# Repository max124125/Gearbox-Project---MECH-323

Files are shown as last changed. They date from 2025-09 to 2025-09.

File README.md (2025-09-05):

# Gearbox Project MECH 323

<p float="left">
  
   
</p>

This project was done throughout the MECH 323 course, and had the goal of designing, assembling and 3D printing a gearbox for a small battery powered model car. 
The gearbox had to be optimized for both a top speed event and ramp climb event, and able to shift between these two gear ratios within only a few seconds of human interaction.

An image and drawing of the gearbox before being placed in the car along with
the final report and CAD files submitted for this project can be found in the section above.

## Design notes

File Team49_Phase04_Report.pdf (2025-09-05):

# Design Project

## MECH 323 Machine Design (Winter 2024) Team 49

## Team

Number | Group 49 - Section 4

## Phase

Number | Phase IIII
Group Members | | Student Number (Required) | Student Name (Optional)
| 1 | 20275181 | Charlotte Kimmins
| 2 | 20208183 | Zoe Glover
| 3 | 20228127 | Maxwell McCutcheon
| 4 | 20298597 | Sebastian Currie

## Mark

i

## Executive Summary

The gearbox design process included the design, fabrication, and assembly of a gearbox to fit into a prefabricated test car and compete in two events, a top speed event and a hill climb event. The design was created through several iterations of modeling and simulation and was optimized into a single stage shifting gearbox that exhibits two gear ratios to effectively compete in both events. Within the project, emphasis was placed on creating a gearbox with high performance metrics while adhering to constraints of the project. The final design included an input and output shaft, two pinions, two gears, bearings, and housing. Within the overall gearbox design, a shifting one stage gearbox was decided to allow for two gear ratios, a high one to maximize torque output for the hill climb, and an inversed low gear ratio to allow for maximum RPM output for the speed event. The housing was important in creating proper fitment of the transmission into the car and worked to balance structural integrity with reducing print time through a series of triangular cut outs. There were two shafts included in the design, an input and an output shaft which were designed with considerations of tolerancing, durability, and performance. These shafts have design features of cylindrical shoulders to hold gears and pinions in place, hex sections on which the gears and pinions lay with a friction fit, and a 20 mm extension from the housing with a D cut shaft to ensure proper alignment of the sprocket and applied torque to the shafts. Additionally, the design features four metal bearings on which the shafts lay which ensures limited friction in shaft rotation. Gears and pinions were chosen for their gear ratio and full depth teeth were used to enhance torque transmission and minimize slippage.

To meet design parameters and to ensure constraints such as successful and consistent performance, low print time, ease of assembly, and scalability of production there were several iterations in the evolution of the gearbox design to reach the final design as described above. Additionally, changes had to be made to the design from the previous theoretical design process and the actuation of printing and assembly. This is inclusive of optimal gear ratios initially being chosen based on performance metrics for both events from initial software modeling, however gear ratios had to be adapted due to modulus limitations and clearance issues during the final CAD preparations. Decisions to adjust the gearbox were carefully considered and weighed against other alternatives to find the best solutions. For the instance of the gear ratios, the team opted to modify the gear ratios rather than adding additional shafts thus maintaining the gearbox integrity. These choices, and the gearbox evolutions were successful and led to performance success in both events.

ii

## Table of Contents

## List of Figures

Figure 1: Fully dimensioned gear and pinion designs. With relevant parameters when machining the

Figure 2: Fully dimensioned drawing of the gear shaft. Drawing includes the front, back and right views,

Figure 3: Fully dimensioned drawing of the pinion shaft. Drawing includes the front, back and right

iii

Figure 4: Orthographic, section, and isometric views of the gearbox with all relevant design criteria shown. Such as design parameters, fully assembled housing dimensions and d-shaft protrusion distance.
| 11
Figure 5: Exploded isometric view of the fully assembled gearbox, highlighting all gearbox parts with
numbers and their respective names and quantities | 12
Figure 6: Fully dimensioned drawing of the housing’s front/ back sides. The drawing includes front, top
and isometric views, highlighting the dimensions for the bushing’s placement | 12
Figure 7: Fully dimensioned drawing of the housings left and right sides. The drawing includes front, top
and isometric views of the part | 13

## List of Tables

Table 1: Sample parts list | 6
Table 2: Technical specifications summary table | 7

## 1.0 Introduction

In the final phase of this project, Phase 4 directed the focus onto modifying the gearbox to be more suitable for 3D printing. Housing for the gear and pinion shafts were designed to meet the dimensional constraints outlined in Phase 1. Modifications of the shaft designs were made to work with a maximum limit of six standard-sized bushings. The keyway features were also changed to hexagonal profiles for better torque transmission. Consequently, the bore holes of the pinion and gear were also adapted to hexagonal profiles to match the shaft designs. This report outlines the evolution of Team 49's gearbox design specifically relating to the transition from AISI 4130 steel to plastic.

## 2.0 Gear Box Design

### 2.1 Overall

This gear box design was created to effectively compete in a high torque hill climb event and a high-speed race event. The design was iterated with factors of performance, durability, design complexity, space constraints, print time constraints and ease of assembly as paramount in the creation of the final gearbox. The finalized design consisted of a one stage shifting gearbox with two shafts, two pinions, and two gears. In this design two gear ratios could be used to optimize the performance in both the hill climb and speed events. Design constraints such as fixed shaft locations, print time, and housing dimensions governed the final design and had implications on specific parameters for the gearbox.

### 2.2 Design

As mentioned above, the overall design is a one stage, shifting gearbox with an input and output shaft and two different gear ratios. This design was chosen to maximize performance in both events, one being a hill climb which required a high output torque, and the other being a speed event, which required a low gear ratio to maximize the output rotation. For success in the hill climb, maximum torque input without causing the DC motor to stall is desired; this in conjunction with a high gear ratio increases the torque on the output shaft which allows the gearbox to climb up the hill. A maximum input torque of 1.9 Nm was used to allow for proper propulsion of the car, without causing the motor to fail, as the motor stall torque is 2.25 Nm. The gear ratio between the pinion and the gear was 2.5, which increased maximized the input torque to 3.01 Nm which led to a theoretical slip angle of 31.3°. In addition to the hill climb, a secondary gear ratio of 0.40 was used for the top speed event. In preliminary design iterations, a gear ratio of 0.61 was chosen, however, as discussed in detail below, physical space constraints and ease of assembly factors led to the top speed gear ratio being the inverse of the hill climb gear ratio. With the same input torque, a low gear ratio allows for a lower input torque and therefore an increased speed. Additionally, by lowering the gear ratio a higher RPM was found for the output shaft which in turn caused faster rotation of the car’s tires, and therefore a faster speed.

### 2.3 Housing

One factor in the gearbox design was the housing in which the transmission components were located. The purpose of the housing was to effectively contain the pinions, gears, and shafts and to have the gearbox fit snugly into the prefabricated car. With this constraint, care was taken to ensure that proper dimensioning and geometry were used in the construction of the housing. There were four bushings located within the housing to fit the input and output shafts on both sides of the housing which worked to reduce the friction on the shafts and housing. An additional consideration for the housing was in the print time required to construct the housing walls. It was important to consider durability in the housing during testing as torque applied to the shafts could apply a force on the housing while balancing the necessity of cutouts to reduce print time. With these factors paramount, triangular cutouts were utilized to maintain the structural integrity of the housing while also reducing print time. Ease of assembly and disassembly was also considered in the design of the housing as the housing repeatedly must be constructed and deconstructed during the geartrain assembly.

### 2.4 Shafts

Two shafts, as input and an output shaft each with a pinion and gear were utilized in the gearbox design. These shafts had several shapes across the length with cylindrical shoulders in place to keep the gears and pinions where desired, hex sections where the pinions and gears sit, and a 20 mm extension from the gearbox housing with a D cut to ensure proper fitment of the sprockets which actuate rotation of the wheels. Tolerance was of importance for the shafts as there were several sections of friction fit along the shaft. These consisted of the shaft inside the bushing, a preset dimension, the pinions and gears on the hex sections, and the sprockets on the D cut shaft extension. Had the shafts been dimensioned improperly, successful performance in events would not be possible. A concern for the shafts was the strength under applied torque, especially in sections, such as the D cut, where the shaft had a small diameter. This is of concern as there is a large, applied torque to the output shaft in the hill climb and an insufficient shaft diameter could lead to shaft failure by mechanism of shear.

### 2.5 Pinions and Gears

The design utilizes two gears and two pinions in the one stage shifting gearbox to transmit torque for each of the events. By using an inverse gear ratio for both events, there is simplicity in production which is an asset for any form of mass production of a gearbox of this design. Additionally, the chosen gear ratios allowed for the use of full depth teeth, rather than stub, as the transmission of torque is not high enough to be of concern for breakage of teeth. This attribute of the pinions as gears has positive effects on the construction of the gearbox as there is increased contact between gears and pinions and there is a decreased risk of slippage, especially when utilizing a friction fit. For the hill climb event, the pinion has eth and the corresponding gear has 37 teeth and the inverse is true for the top speed event.

### 2.6 Additional Performance Parameters

A module of 1.5 mm was utilized for the gearbox design. This module allowed for an increased number of teeth on the gears and pinions without a notable increase in the physical space consumed by each member. Additionally, in the gearbox design a pressure angle of 20 ˚ which represents the angle between the tooth face and the gear wheel tangent, dictating the point of impact for applied tangential load. With a standard gearbox design with curved teeth this pressure angle is the most appropriate to avoid an increase in applied radial force which could lead to failure in the teeth.

Overall, the gearbox design is intended to function with high performance in both events, with a low print time and with a high degree of reliability. Through the one stage shifting gearbox a variety of performance metrics can be met while adhering to constraints of physical space and ensuring ease of assembly and disassembly, which is impactful for scalability of the design.

## 3.0 Evolution of Gear Box

### 3.1 Initial Design Choices

Early in the design process it was decided to make the gearbox a 1 stage shifting design. The main reason for this was that it would reduce mechanical losses in the system. These reduced losses would be in the form of less shafts being needed, and therefore less frictional resistance between shafts and bushing, along with less contact/sliding friction between the teeth of gears. For example, in a basic one stage gearbox design only two shafts are needed, and therefore losses come from 4 bushings and 1 location of contact friction between gears. In a two-stage gearbox, these losses are increased to 6 bushings and 2 points of contact friction between gears. This is a 50% increase in bushing losses and a 100% increase in gear contact losses.

Furthermore, when using the motor torque graph, and having to account for 10 Newtons of expected losses, excluding the gearbox, it was figured that there was minimal room to work with in terms of adding losses, as with too much additional friction the gearbox simply might not run. The only reason to have potentially strayed from a 1 stage shifting, would have been if the gearbox parameters simply did not allow the optimized gear ratios (or something close them) to fit. This likely would be in the form of interference with the gearbox’s 10x10 mm cutouts placed at the top and bottom of case, or if a gear/pinion had to stick more than 10 mm out from the gearbox’s sides. These key points of interference mostly limited very high or low ratio, where one gear/pinion had to be significantly larger than the other. However, weather this was an issue would be found out as the optimized ratios were decided and the calculations on gear/pinion sizes were made.

### 3.2 Weights and gear ratio choices

During the writing of phase 1 the option of adding weights to the car was given, this was a key design choice and would greatly affect the cars performance. To figure out the ideal choice, the optimal ratios for all 8 possible scenarios were done (each event with four possible weight options.
In doing this it was found that by adding just one weight to the car it was expected to slow the top speed event from 2.7 second, down to 3.5 seconds (an increase of 30%) This change was even more pronounced with adding a second and third weight, where the car would slow down even further all the way to 6.5 seconds. Meanwhile, at its base weight the car was expected to reach 31.1 degrees in the hill climb, but with the addition of all three weight the expected peak hill climb angle would only increase to approximately 35 degrees. For this reason, no weights were decided on at all, as it seemed to drastically hurt the top speed event but only yield minimal improvement in the hill climb. As such, the car would mainly be optimized for top speed.
With this decided, it was found that a gear ratio of 0.61 was optimal for the speed event while a ratio of 2.5 was optimal for hill climb.

However, as additional calculations were done, slight further changes were found to be need. First and foremost, the gear ratios were found not to be achievable, this was due to modulus limitations and other design parameters. As such they had to be modified slightly and instead ratios of 0.636 and 2.467 (in place of 0.61 and 2.5 respectively) were planned for. This translated to 11 and 7 teeth for the top speed event and 15 and 37 teeth for the hill climb event. At the time this was believed to be the final major design choice needed, with much of the timeline moving forward spent on analysis.

### Calculations

Now that a gearbox was designed, in depth calculations were needed to ensure that everything functioned correctly. The first set of calculations included the torques and forces at play in the system. With these it was determined that the maximum torque anywhere in the system would be on the output shaft at 2.43 Nm. This torque would occur during the hill climb event, right before stall. Furthermore, the gear teeth would also be facing their peak force at this time of 127.65 Newtons.
To ensure that everything would function correctly, factors of safety were to be determined for both gear and pinion of the hill climb.

These calculations took into account many factors. The first of these is the quality index, a measure of what accuracy is needed in such a system. Since this is a small RC car, that doesn’t require high accuracy precision in starting/stopping, it was placed at a level 8, putting it in a similar category as a small power drill. Another such factor is the rim thickness factor, a determinant of the distance between the gear dedendum circle and the outer shaft hole. This measure considers gears that have too thin of a wall, and as such might result in premature warping or cracking. One of the most significant factors in a scenario such as this is the overload factor, this considers any sharp shocks that might be placed in the system. If for example, the car suddenly hit a wall after moving at full speed, a very high force would be placed on the gears for a split second, and, if not accounted for could make them fail. Fortunately, all the scenarios the car would be driven in were known, and no such shocks would be present.

All of these factors and more helped to calculate a resultant factor of safety for bending fatigue failure and for contact/pitting failure. These were calculated for both gear and pinion with the goal of having the lowest FOS be 1.50. Since many of the parameters are already decided, such as material strength, hardness, cycles, etc., very little can be change if one of the safety factors lower than desired. As such, the only factor that can be edited to maintain the systems integrity, is face width. As such, all of the calculations were run at 7 mm face width and then increased until the factors of safety reached a minimum of 1.50. This trial and error could have resulted in another issues, as if the minimum face width was too wide, there would not be enough room in the gearbox to shift between ratios. Fortunately, this did not become a problem and a final face width of 13 mm was ideal.

### 3.3 Final Cad for Printing

Unfortunately, during the final CAD preparation, a slightly clearance was found. Where the larger gear/pinion of each ratio interfered with the 10x10mm cutouts placed at the top and bottom of the gearbox. As aforementioned, these could not be obstructed and were required for mounting the gearbox in the car. At this point, two options were given for the group, either modify the gear ratios so that they no longer interfere with the cutouts, this would be in the form of having to reduce them (i.e. reduce size of larger gear/pinion, and then increase size of the opposing gear/pinion). Or, the second option was to keep the calculated gear ratios, but this would require adding an extra shaft to the gearbox (converting it to a two stage), this would allow for the gear reduction/increase to be done in steps with smaller gears.

Ultimately the group decided on option 1, as it meant the least amount of the overall design had to be changed. Allowing the previously designed frame, shafts, gear widths, number of gears, and shifting method to all be kept the same. Furthermore, this option allowed the gearbox to stay in line with the main design choice of trying to reduce mechanical losses. Which as aforementioned if an extra shaft had to be added, it would add significant losses into the system. As such, the only design change made was to the number of teeth on each pinion/gear. This meant that the ratios had to be slightly adjusted, but kept the rest of the design the same. Furthermore, by choosing this option, most of the calculations done in previous reports were still valid, with the added benefit of some becoming even more favorable. Such as the factor of safety, where having to slightly reduce the gear ratios reduced the torque in the secondary shaft (mainly for hill climb) and made the design stronger.

Overall, these design choices proved to be well founded. And, in the hill climb, the wheels of the car started to only slip slightly, right as it reached stall height. This was the goal for this challenge and placed the team 18th.
In the top speed event similarly, promising results showed. With a faster than expected speed of 1.700 seconds, placing the team 11th overall, and only 0.28 seconds behind first place.

## 4.0 Technical Specifications

### 4.1 Assembly Instructions

4.1.1 Parts List
All parts necessary for assembly of the gearbox can be found in Table 1, within 4.2 Technical specifications summary. These parts include to assemble the gearbox are as followed: two 17-tooth pinions, two 37-tooth gears, a gear shaft, a pinion shaft, one front housing, one back housing, one right housing, and one left housing, and 4 bushings.

4.1.2 Tools Required
Within the construction of the gearbox sandpaper was used to ensure proper fitment of all gears and pinions on shafts and to allow for a friction fit of shafts to bushings. No other tools were required for assembly of the gearbox, as high tolerance fits were used to connect all sides of the housing, as well as shoulders to prevent the bushings from sliding out.

4.1.3 Assembly Summary
The gearbox was designed to be assembled by hand without the use of tools. Depending on the 3D printer resolution, some pieces will need some minor sanding to achieve the optimal fit and to fit within the filament. Steps take to assemble the gearbox are:
1- Place the both the front and back of the gearbox onto a solid surface with the shoulder of the shaft holes on the side of the housing resting on the surface. Place one bushing inside each hole, and ensure they are fully pressed into the housing.
2- Orient the pinion shaft so the d-shaft is on the right side. Slide a pinion onto the left side of the shoulder, making sure the hexagon of both pieces are aligned. Then slide a gear onto the right side of the shoulder. Again, making sure both hexagons are aligned before applying force.
3- Orient the gear shaft so the d-shaft is on the right side when looking at it. Then slide the second gear all the way to the shoulder, making sure both hexagons are aligned. Then slide the second pinion all the way down the shaft, but stopping before the gear and pinion touch, making sure both hexagons are aligned.
4- While both shafts are still oriented to have the d-shaft on the right side, place the left side of both assembled shafts into the holes on the back housing. Making sure they fit withing the inner diameter of the bushings. Noting that the pinion shaft is in the hole on the left side of the housing.
5- Attach both the left and right housings to the back housing by snapping the prongs into their respective slots. Ensuring that the right and left housings are flush with the back housing.
6- Attach the front housing to the rest of the assembly, making sure that the shoulder of the shaft holes are facing outwards before sliding the d-shaft through. As well as ensuring that the right and left housings are flush with the front housing after attachment.
7- Check that both shafts can spin freely, and that both sets of gears can interface correctly, while also being able to be connected and disconnected smoothly.

### 4.2 Technical Specification Summary

Table 1: Sample parts list

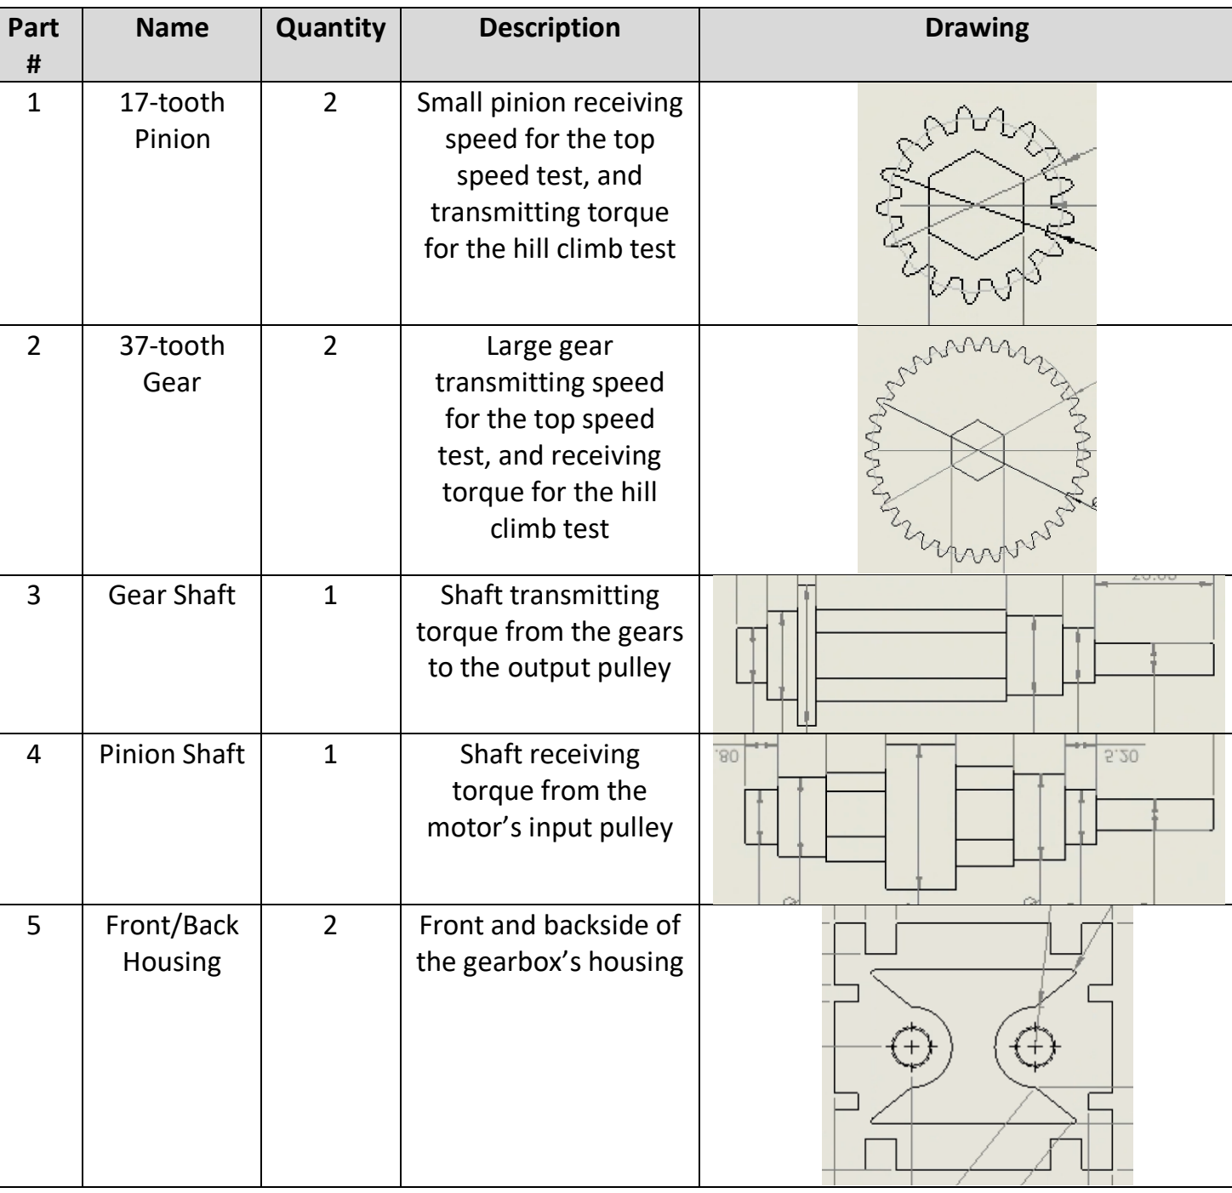
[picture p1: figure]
Part #; Name; Quantity; Description; Drawing

1 | 17-tooth Pinion | 2 | Small pinion receiving speed for the top speed test, and transmitting torque for the hill climb test
2 | 37-tooth Gear | 2 | Large gear transmitting speed for the top speed test, and receiving torque for the hill climb test
3 | Gear Shaft | 1 | Shaft transmitting torque from the gears to the output pulley
4 | Pinion Shaft | 1 | Shaft receiving torque from the motor’s input pulley
5 | Front/Back Housing | 2 | Front and backside of the gearbox’s housing

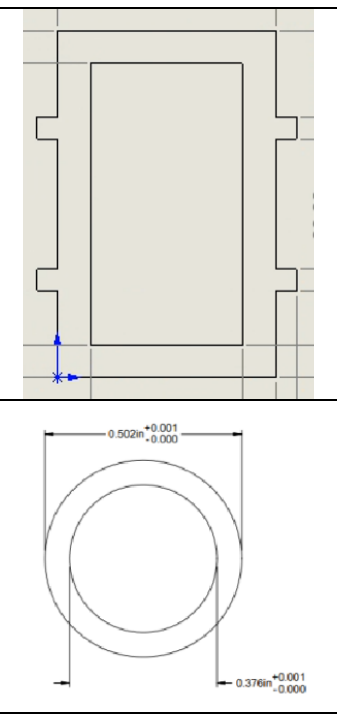
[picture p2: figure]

6 | Left/Right Housing | 2 | Left and right side of the gearbox’s housing
7 | Bushing | 4 | Bushings to allow the shafts to rotate with minimal resistance

Table 2: Technical specifications summary table
Gearbox Technical Specifications | Value | Units
Gearbox Type | Stage 1 | -
Motor Operating Torque – Hill Climb | 1.9 | Nm
Motor Operating Torque – Top speed | 1.9 | Nm
Pinion Lowest Safety Factor | 10.3 | -
Gear Lowest Safety Factor | 23.3 | -
Gear Ratio – Hill Climb | 2.5 | -
Gear Ratio – Top Speed | 0.4 | -
Print Time | 7.32 | Hours
Gearbox Footprint (L*W*H) | 432000 | mm

## 5.0 Future Work Recommendations

Given the limited twelve-week timeframe allocated for this project, the complexity and scope of development were constrained; however, for future iterations of this project, there are several recommendations aimed to optimize the vehicle performance. Transitioning from a single-stage gearbox to a two-stage gearbox is highly recommended as this would allow for higher gear ratios that would optimize torque output for both events. Further analyses and simulations to optimize gear ratios for the specified events could enhance power transmission efficiency and overall performance. The utilization of helical gears would also be recommended, as this shape increases the strength and can handle greater loads compared to spur gears. One may also consider integrating some sort of lubrication system to help maintain its functionality over a longer period, ultimately reducing wear and minimizing the risk of component failure. Lubrication will also reduce friction, resulting in smoother operation and prolonged gearbox lifespan. The exploration of other materials and manufacturing techniques would also be advised. The adoption of materials with better mechanical properties could improve strength-weight ratios. Another future consideration would be to refine the layout and packaging of the gears, bearings and shafts to minimize weight and reduce mechanical losses. Finally, more testing and validation of the designed gearbox would help provide valuable insights into the performance and reliability of the gearbox design facilitating further refinement.

## 6.0 Conclusion

Upon development a gearbox suitable for high torque hill climb and top speed events. Transitioning from AISI 4130 steel to plastic for the gearbox involved modifications to the CAD schematics to accommodate for 3D printing, while maintaining functionality and reliability. Key design choices such as opting for a one-stage shifting gearbox to reduce mechanical losses between events, and optimizing gear ratio for different events, contributed to the overall success of the project.
Despite encountering challenged during the final CAD preparations before printing, informed decisions allowed for the insurance that the gearbox designing not only aligned with objectives set, but also allowing it to fit together smoothly. Opting for designs which allowed for minimal changes to the overall design without major mechanical losses. Allowing for the maximum achievable results in both the hill climb and top speed events.
Future recommendations for the future iterations of this project include transitioning to a two-stage gearbox, allowing for higher gear ratios to be achieved. While also exploring the use for helical gears, increasing the strength of the design, or even lubricating the system to improve performance and longevity should the gearbox be in constant use. Lastly refining the layout and the overall packaging of components to minimize the weight and decrease any mechanical losses there might be. Further testing of the gearbox design will be essential for continuation and improvements for the optimal performance and reliability in the future.

## References

## Appendix A – Drawing Package

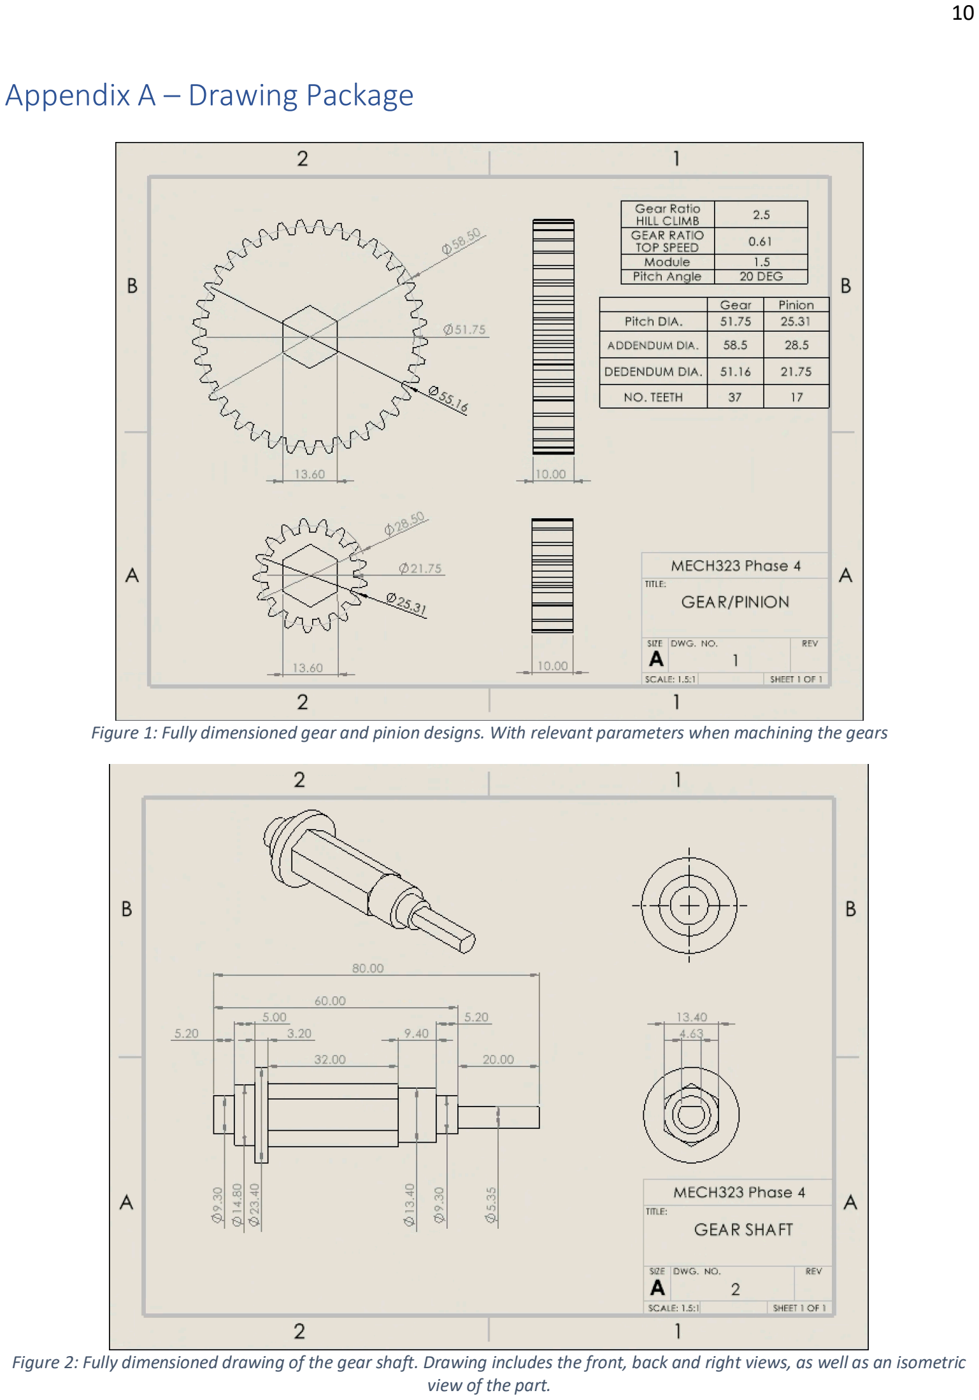
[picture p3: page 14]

Figure 1: Fully dimensioned gear and pinion designs. With relevant parameters when machining the gears

Figure 2: Fully dimensioned drawing of the gear shaft. Drawing includes the front, back and right views, as well as an isometric view of the part.

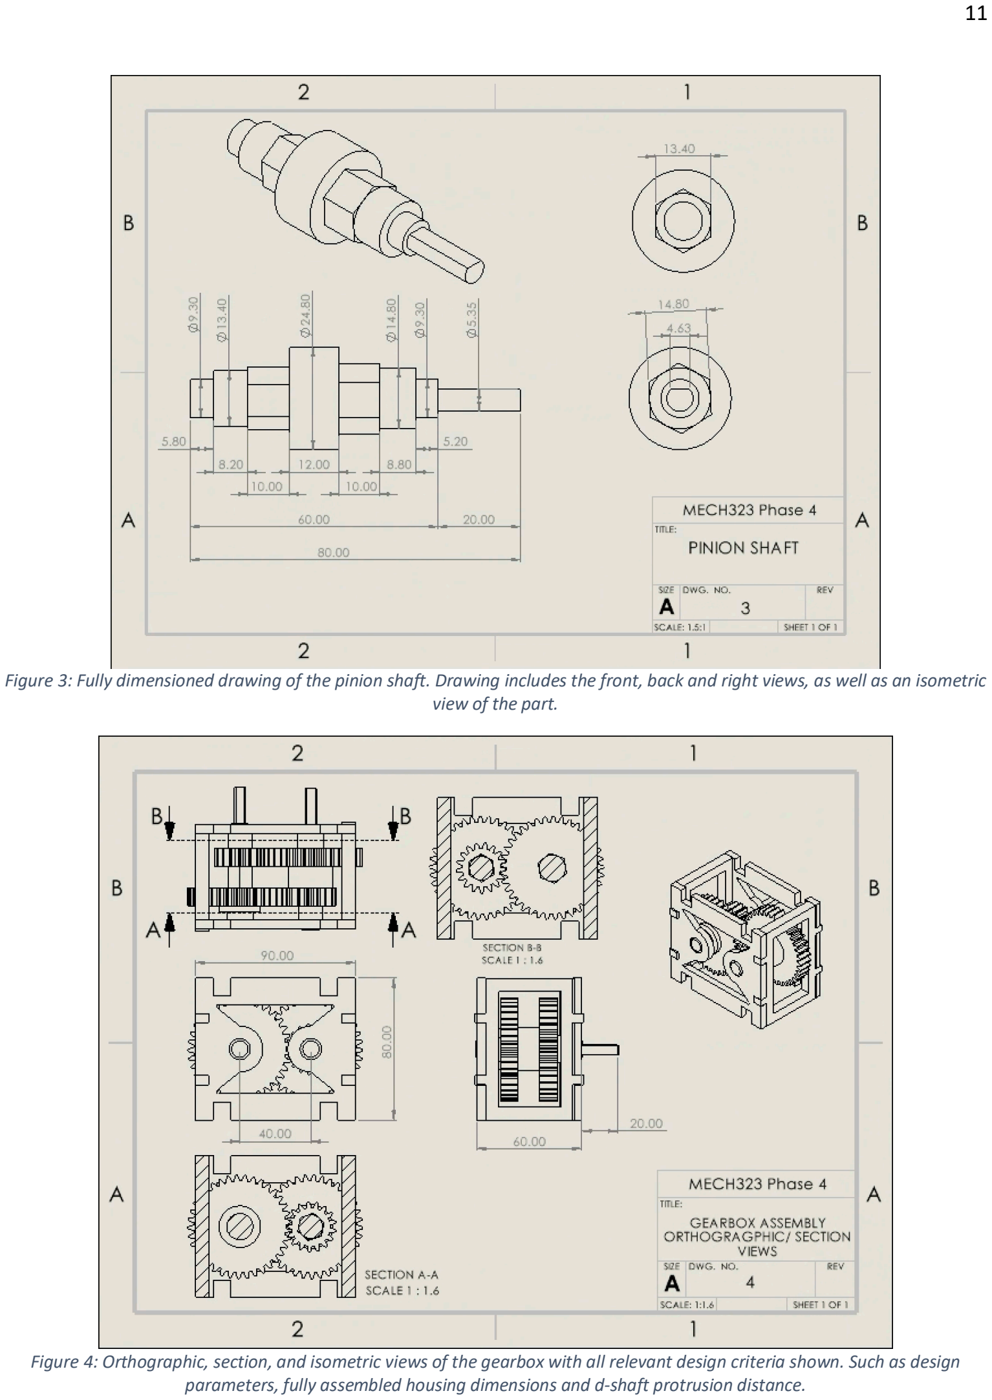
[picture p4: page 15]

Figure 3: Fully dimensioned drawing of the pinion shaft. Drawing includes the front, back and right views, as well as an isometric view of the part.

Figure 4: Orthographic, section, and isometric views of the gearbox with all relevant design criteria shown. Such as design parameters, fully assembled housing dimensions and d-shaft protrusion distance.

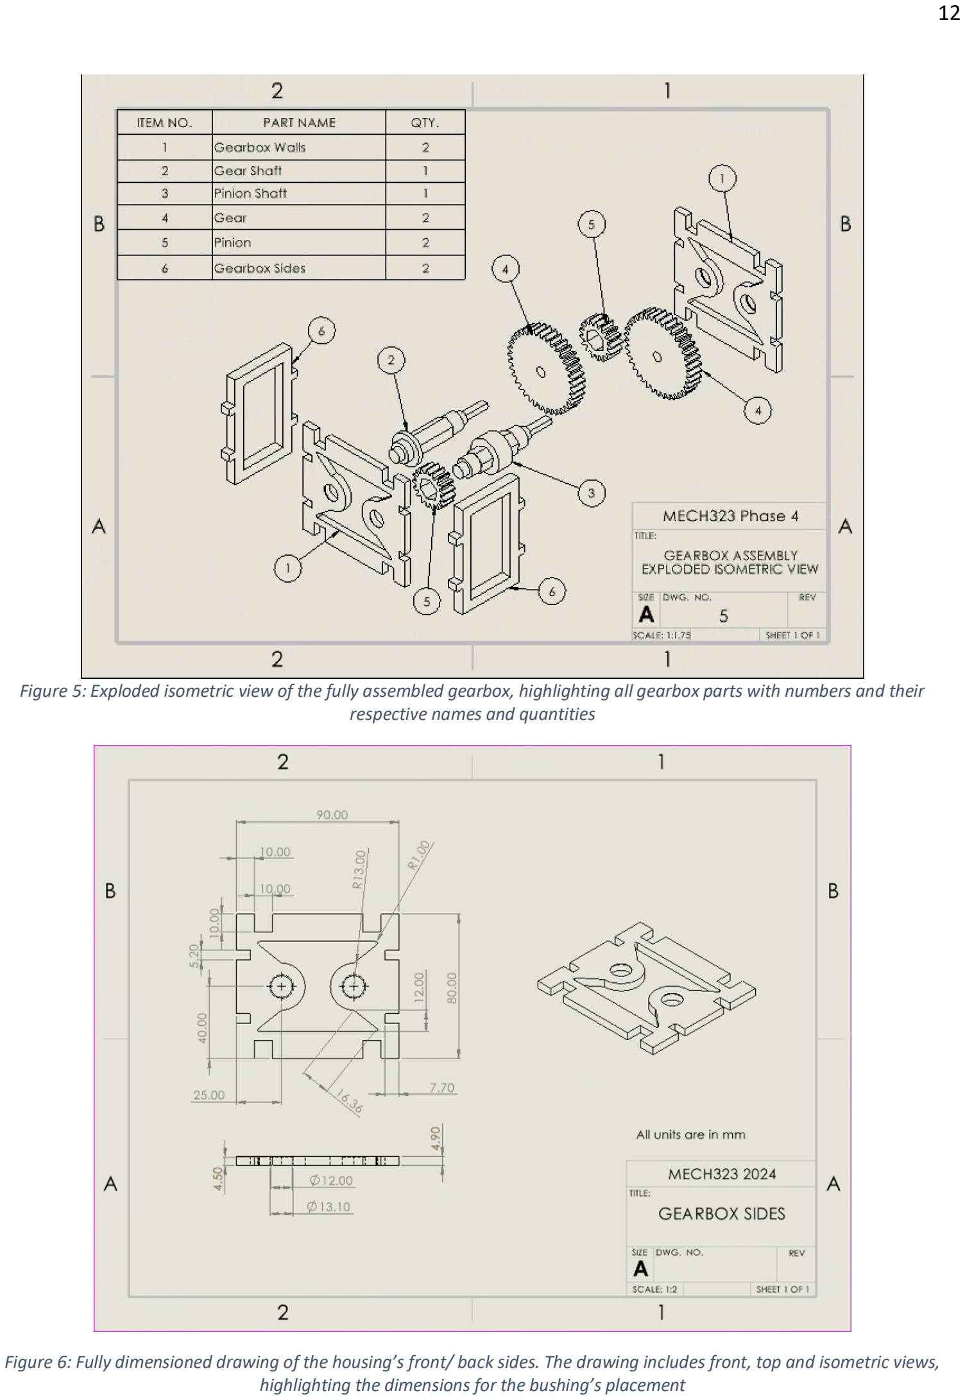
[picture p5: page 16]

Figure 5: Exploded isometric view of the fully assembled gearbox, highlighting all gearbox parts with numbers and their respective names and quantities

Figure 6: Fully dimensioned drawing of the housing’s front/ back sides. The drawing includes front, top and isometric views, highlighting the dimensions for the bushing’s placement

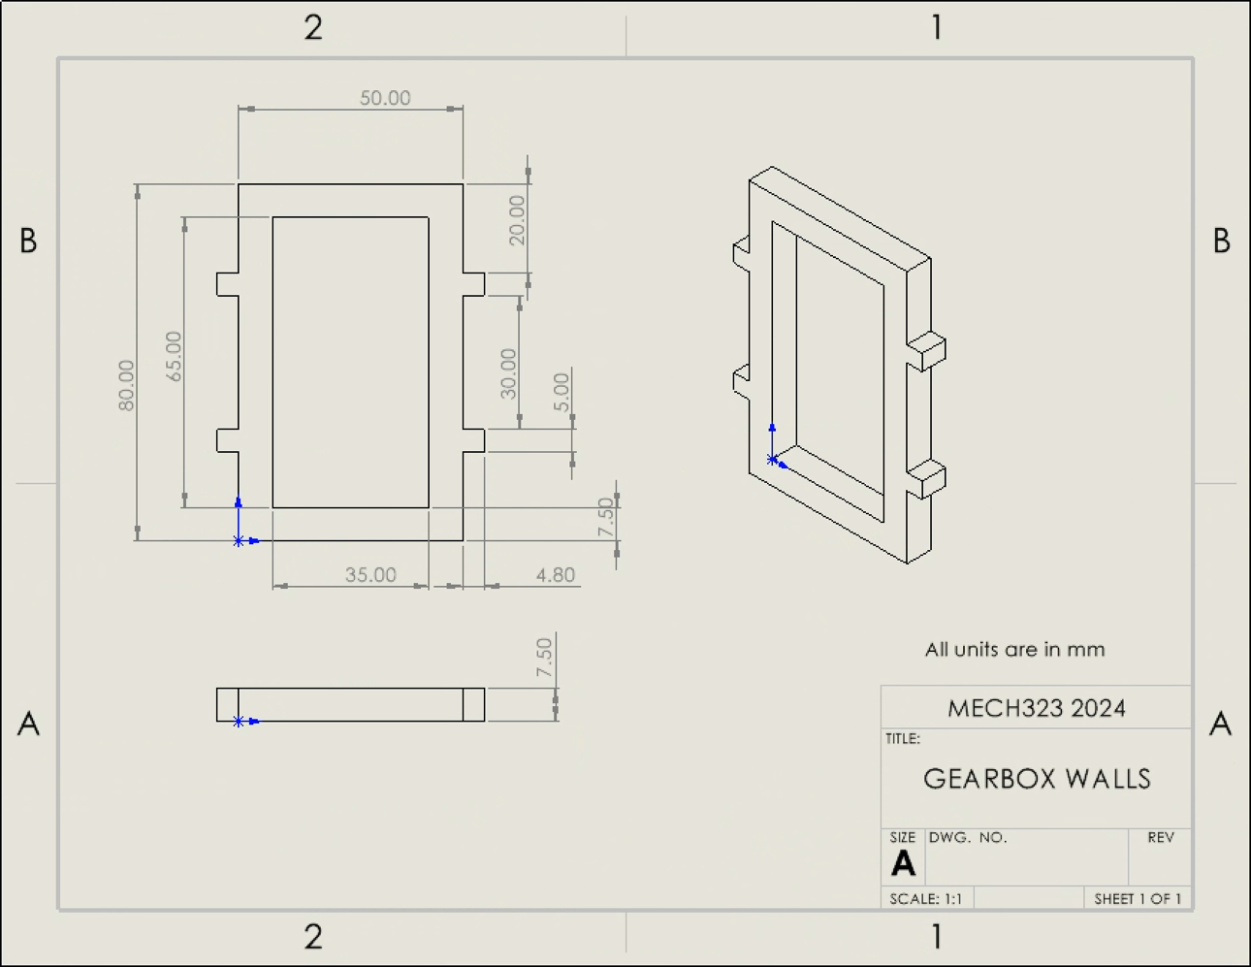
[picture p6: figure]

Figure 7: Fully dimensioned drawing of the housings left and right sides. The drawing includes front, top and isometric views of the part.

# Phase 4 Summary Page

(Attach to the end of your Phase 4 Report on a separate page)

## Team

Number | 49

## Phase

Number | IIII

# Global Design Characteristics

Gear Box Parameters | Number of Stages | 1
| Speed Gear Ratio | 2.5
| Hill Climb Gear Ratio | 0.4
Vehicle Weights | Total Number of Weights | 0

# Predicted Event Performance

Speed Event | 3m Top Speed Zone Time (s) | 1.7
| Top Speed (m/s) | 1.1
| Motor Operating Torque (Nm) | 1.9
| Motor Operating Speed (rpm) | 50
Hill Climb Event | Distance (m) | 0.57

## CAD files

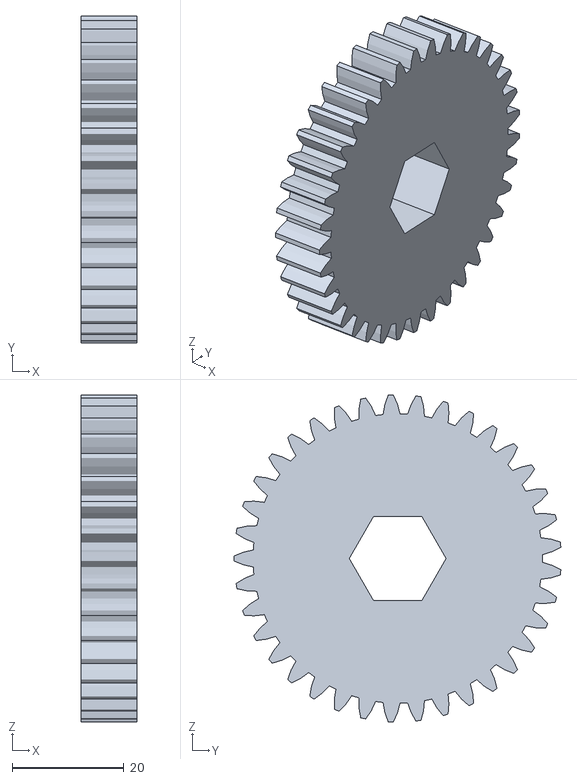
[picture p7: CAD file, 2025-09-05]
Gear.STL
10.0 x 58.4 x 58.5

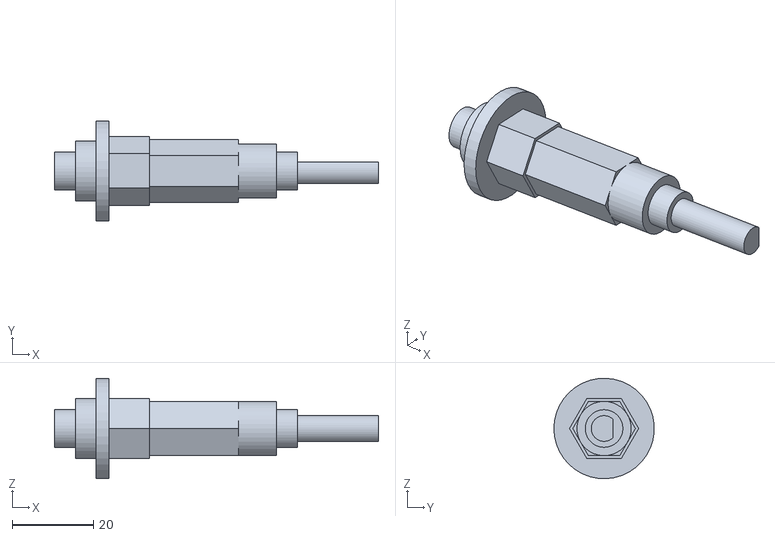
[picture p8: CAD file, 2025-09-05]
Gear Shaft.STL
80.0 x 24.8 x 24.8

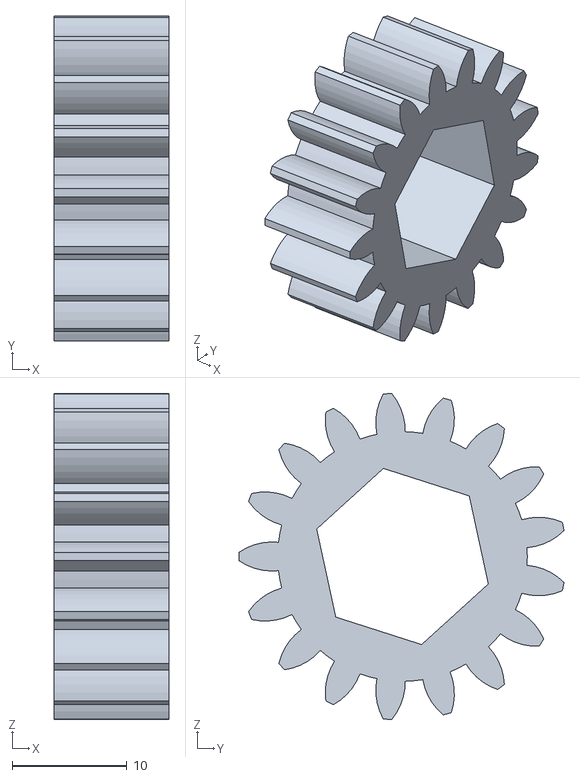
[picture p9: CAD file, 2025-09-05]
Pinion.STL
10.0 x 28.3 x 28.4

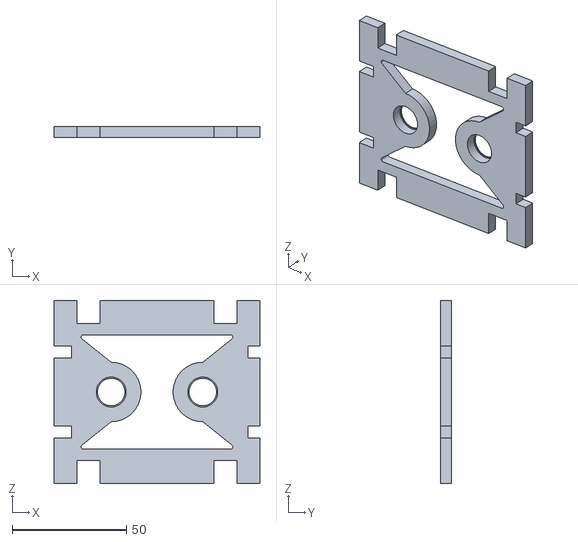
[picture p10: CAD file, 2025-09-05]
Walls.STL
90.0 x 4.90 x 80.0

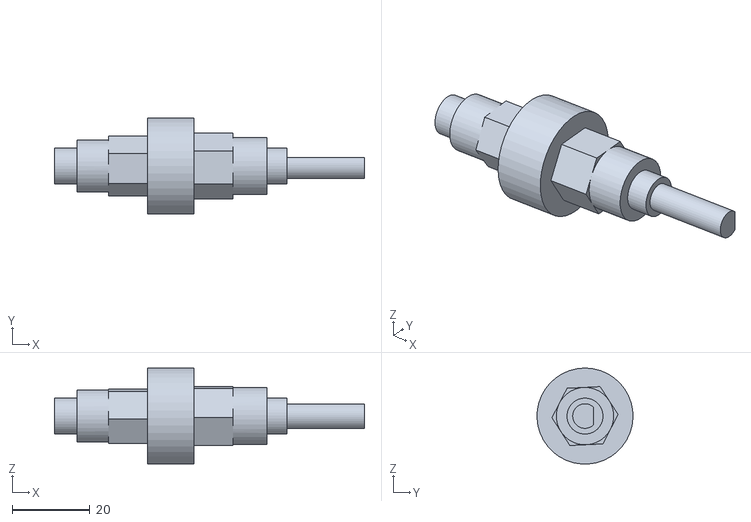
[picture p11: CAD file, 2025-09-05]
Pinion Shaft.STL
80.0 x 24.8 x 24.8

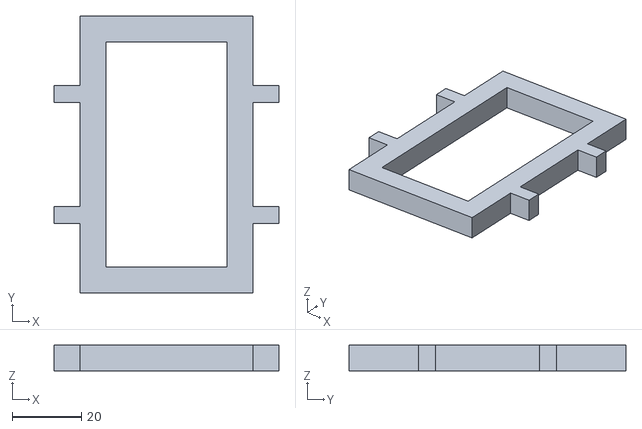
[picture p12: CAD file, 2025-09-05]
GearboxSide.STL
65.0 x 80.0 x 7.50
